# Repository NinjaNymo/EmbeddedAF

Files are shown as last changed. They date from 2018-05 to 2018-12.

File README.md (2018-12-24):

# EmbeddedAF
This repository contains the source code and hardware design files for a indoor automated urban farming system. 

The system has a master/slave architecture, where the master is refered to as the _master_, while the slaves as the _nodes_.

### **_The Concept:_**
The idea was to use a wireless sensor network system as a case study in an embedded systems development process.

Due to the master/slave architecture of the system, the project covers both embedded C development on the node devices and embedded Linux development on the master device, as well as communication over ZigBee between the two.

All in all; a good variation of challanges to learn more about embedded systems.

### **_The Node:_**
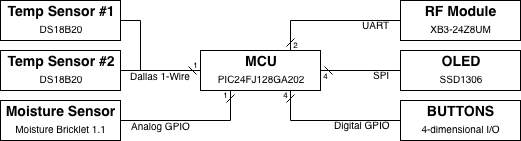
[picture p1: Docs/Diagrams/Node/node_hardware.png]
Node Structure


The node features a 16-bit MCU and a XBee 3 ZigBee module on an in-house developed and etched PCB. An OLED display and buttons are included on the board such that the node device can be used in an _offline mode_ independetly of the master device.

The node device measures temperature on the PCB and interfaces with 1) external digital temperature sensors, 2) an external analog soil moisture sensor and 3) an external relay that controls a grow-light.

The idea is to control the grow-light on a day/night-like cycle and record and publish the temperature and soil moisture measurements to the master device.

* The firmware is written in C, and can be found in [/src/node/](/src/node).
* The schematic and PCB is designed in Eagle, and can be found in [/Eagle/node/](/Eagle/node/).

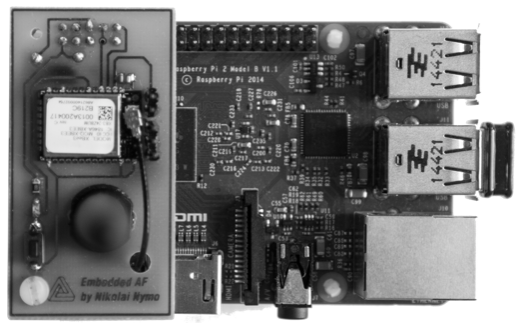
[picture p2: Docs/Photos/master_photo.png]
Master PCB
 

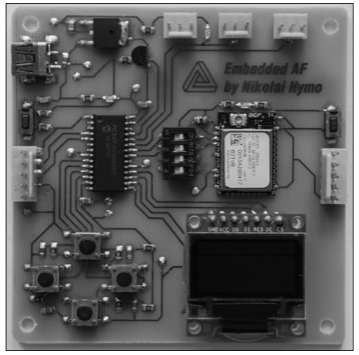
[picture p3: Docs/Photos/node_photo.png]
Node PCB Node PCB


Master Structure
This repository contains stuff for a project on embedded automatic farming.

That includes circuit schematics, PCB designs and code to run on the two systems:

1. **The node:** A board with a 16-bit MCU and a XBee 3 micro module. It features two temperature sensors and one analog soil moisture sensor as well as I/O for offline availiability. The source found in src/node is written C and compiles with XC16.
2. **The master:** A Raspberry Pi 2B mounted with the same XB3 modules as the nodes. It runs Raspbian Stretch lite, a MQTT broker, a Node.js server that provides a web ui and finally a MQTT-SN gateway that is implemented in python and who's source code is found in src/master.

In addition there are some random python scripts, diagrams in the DrawIO folder, prototype schematics and board designs.

### The concept:

The idea here is to use a wireless sensor network system inteded to be used in indoor automatic farming as a case study in a development process.

I like watching things grow, and I think indoor has interesting benefits over traditional outdoor farming such as reduced water consumption, seasonal independence and a shorter logistic travel distance so perhaps some day all this might turn into something.

To do automated farming, it controls a LED lamp on a day/night-like cycle which can be configured through the on-board user interface or wirelessly.

The lamp and power distribution needs some work and will be put up here once it is up to spec. 

Further the node measures water content in soil which is intended to be used with automated watering. It has a Dallas 1-wire bus on one of it connectors which currently run both an on-board temp sensor and an external waterproof one that I planned on sticking in the soil.

The MCU does everything mentioned above, and UARTs with the XB3 which handle MQTT over ZigBee.

With many of these and an online master device from which you can monitor and control the whole setup it should be possible to realize indoor automated farming.

### Technical details:

#### The node:
* Microchip PIC24FJ128GA202 MCU. 16-bit.
* Digi XB3-24Z8UM RF module running ZigBee 3.0 API as a router.
* Maxim DS18B20 temperature sensors.
* Analog capacative soil moisture sensor.
* SSD1306 OLED display driver.
*

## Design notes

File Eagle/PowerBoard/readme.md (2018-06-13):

### Resources:
* [Relay switch circuits.](https://www.electronics-tutorials.ws/blog/relay-switch-circuit.html)
* [G5LE relay @ DigiKey.](https://www.digikey.com/product-detail/en/omron-electronics-inc-emc-div/G5LE-14-DC3/Z3326-ND/1815628)

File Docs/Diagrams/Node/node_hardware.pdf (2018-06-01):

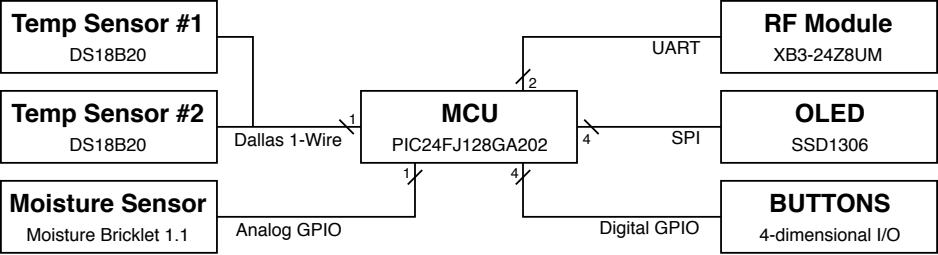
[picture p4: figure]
MCU; PIC24FJ128GA202; RF Module; Temp Sensor #1; Temp Sensor #2; Analog GPIO; Moisture Sensor; Moisture Bricklet 1.1; OLED; SSD1306; BUTTONS; 4-dimensional I/O; Dallas 1-Wire; SPI 4; Digital GPIO; UART

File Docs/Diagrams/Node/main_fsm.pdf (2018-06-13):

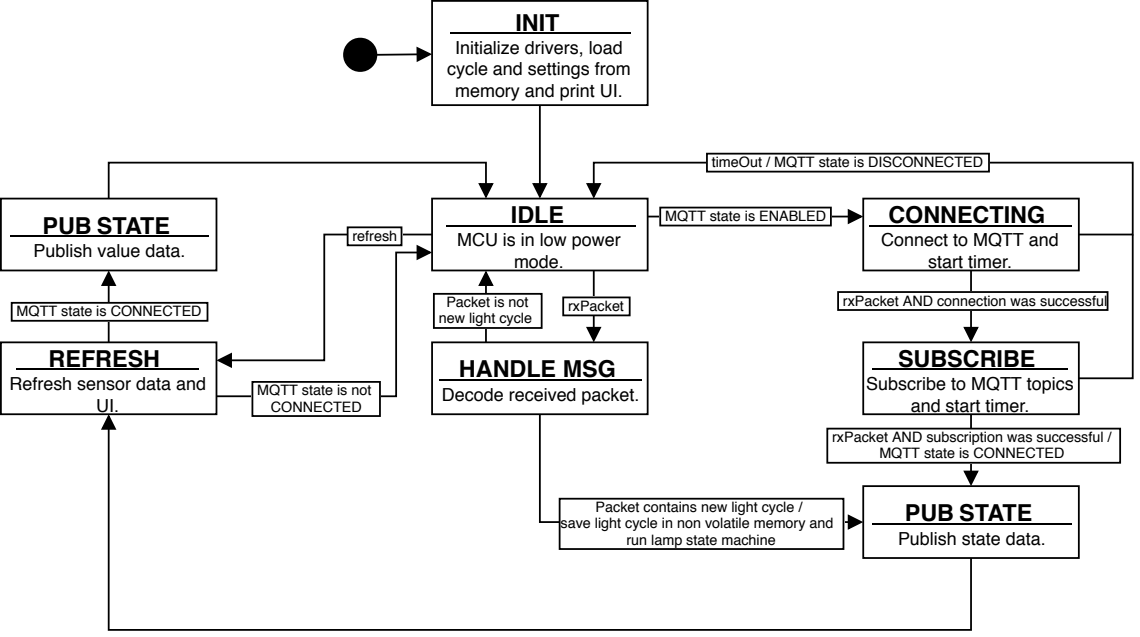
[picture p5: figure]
MQTT state is ENABLED; rxPacket; refresh; IDLE; MCU is in low power mode.; rxPacket AND connection was successful; timeOut / MQTT state is DISCONNECTED; CONNECTING; Connect to MQTT and start timer.; MQTT state is CONNECTED; SUBSCRIBE; Subscribe to MQTT topics and start timer.; PUB STATE; Publish state data.; Packet is not new light cycle; Packet contains new light cycle /; run lamp state machine; HANDLE MSG; Decode received packet.; MQTT state is not CONNECTED; REFRESH; Refresh sensor data and UI.; Publish value data.; INIT; Initialize drivers, load cycle and settings from memory and print UI.

rxPacket AND subscription was successful /

save light cycle in non volatile memory and

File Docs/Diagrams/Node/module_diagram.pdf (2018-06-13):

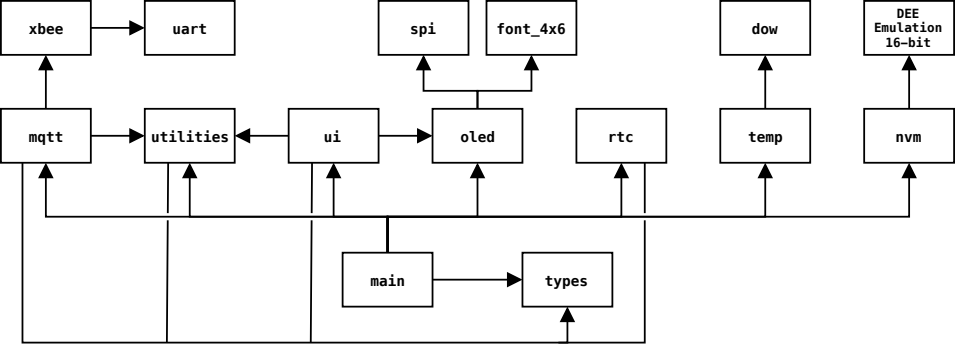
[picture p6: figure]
spi; oled; dow; temp; xbee; mqtt; utilities; rtc; uart; nvm; DEE Emulation 16-bit; font_4x6; main; types

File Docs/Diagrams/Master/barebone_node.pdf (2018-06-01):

MCU
Microchip
PIC24FJ128GA202

RF Module
Digi
XB3-24Z8UM

Temperature 1
Maxim Integrated
DS18B20

Temperature 2
Maxim Integrated
DS18B20

Water
Tinkerforge
Moisture Bricklet 1.1

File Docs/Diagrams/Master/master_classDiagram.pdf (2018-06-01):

«Class»
digi:xbee:devices:ZigBeeDevice
on_connect | : function*
on_message | : function*
on_subscribe : function*
on_disconnect : function*
__init__(port:string, baud_rate:integer)
open()
add_data_received_callback(function*) send_data(remote_xbee_device:ZigBeeDevice, data:bytearray) get_64bit_addr() : bytearray

«Class»
lib:threading:Thread
daemon : bool
name : string
start()

«Class»
MSG
sender : ZigBeeDevice
data : bytearray

«Class»
Gateway
inQ | : Queue
outQ | : Queue
XBH | : XBeeHandler
clientList : NodeClient[0..*] __init__(uartPort:string)
start()
stop()

«Class»
NodeClient
inQ | : Queue
outQ | : Queue
stop | : bool
nodeID : string
device : ZigBeeDevice
mClient : Client
__init__(device:ZigBeeDevice, outQ:Queue, nodeID:string)
run()
connect(keepAlive:integer)
connectedCB(client:Client, userdata:null, flags:dict, rc:integer) subscribe(topic:string)
subscribedCB(client:Client, userdata:null, mid:integer, granted_qos:integer) publish(msg:MSG)
messageCB(client:Client, userdata:null, msg:mqtt_msg)
disconnect()
disconnectedCB(client:Client, userdata:null, rc:integer) put(msg:MSG)
terminate()

«Class»
XBeeHandler
inQ | : Queue
outQ | : Queue
device : ZigBeeDevice
__init__(inQ:Queue, outQ:Queue, XBeePort:string) run()
receiveCB(xbee_message:XBeeMessage) terminate()

«Class»
paho:mqtt:client:Client
on_connect | : function*
on_message | : function*
on_subscribe : function*
on_disconnect : function*
connect(host:string, port:integer, keepAlive:integer) subscribe(topic:string)
publish(topic:string, data:integer) publish(topic:string, data:string)
loop_start()
loop_stop()
disconnect()
1 | 1 | 1 | 1
1 | 0..*

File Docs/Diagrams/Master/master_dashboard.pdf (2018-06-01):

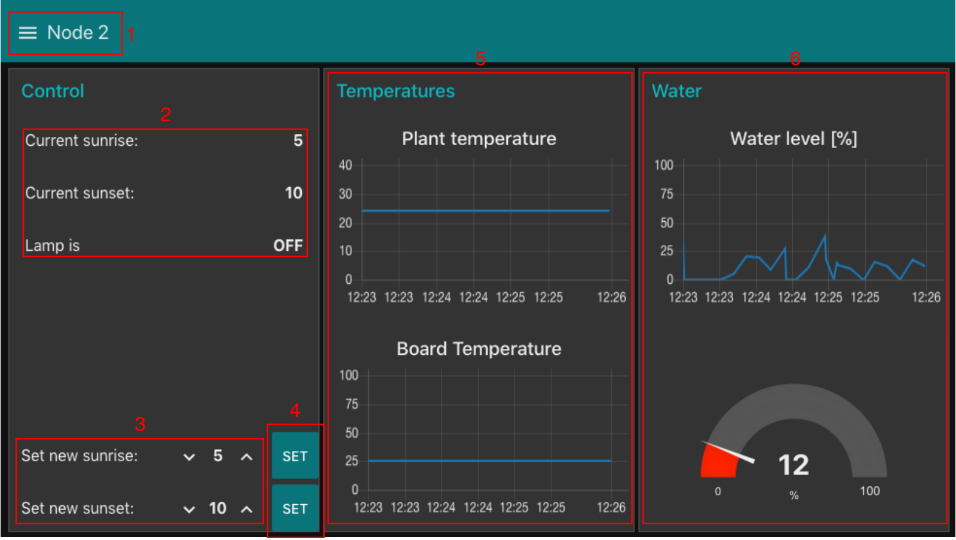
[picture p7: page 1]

1

2

3

4

5

6

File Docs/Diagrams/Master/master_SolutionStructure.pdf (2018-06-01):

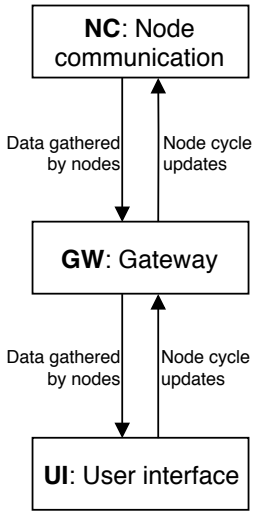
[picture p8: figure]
NC: Node communication; GW: Gateway; UI: User interface; Node cycle updates; Data gathered by nodes

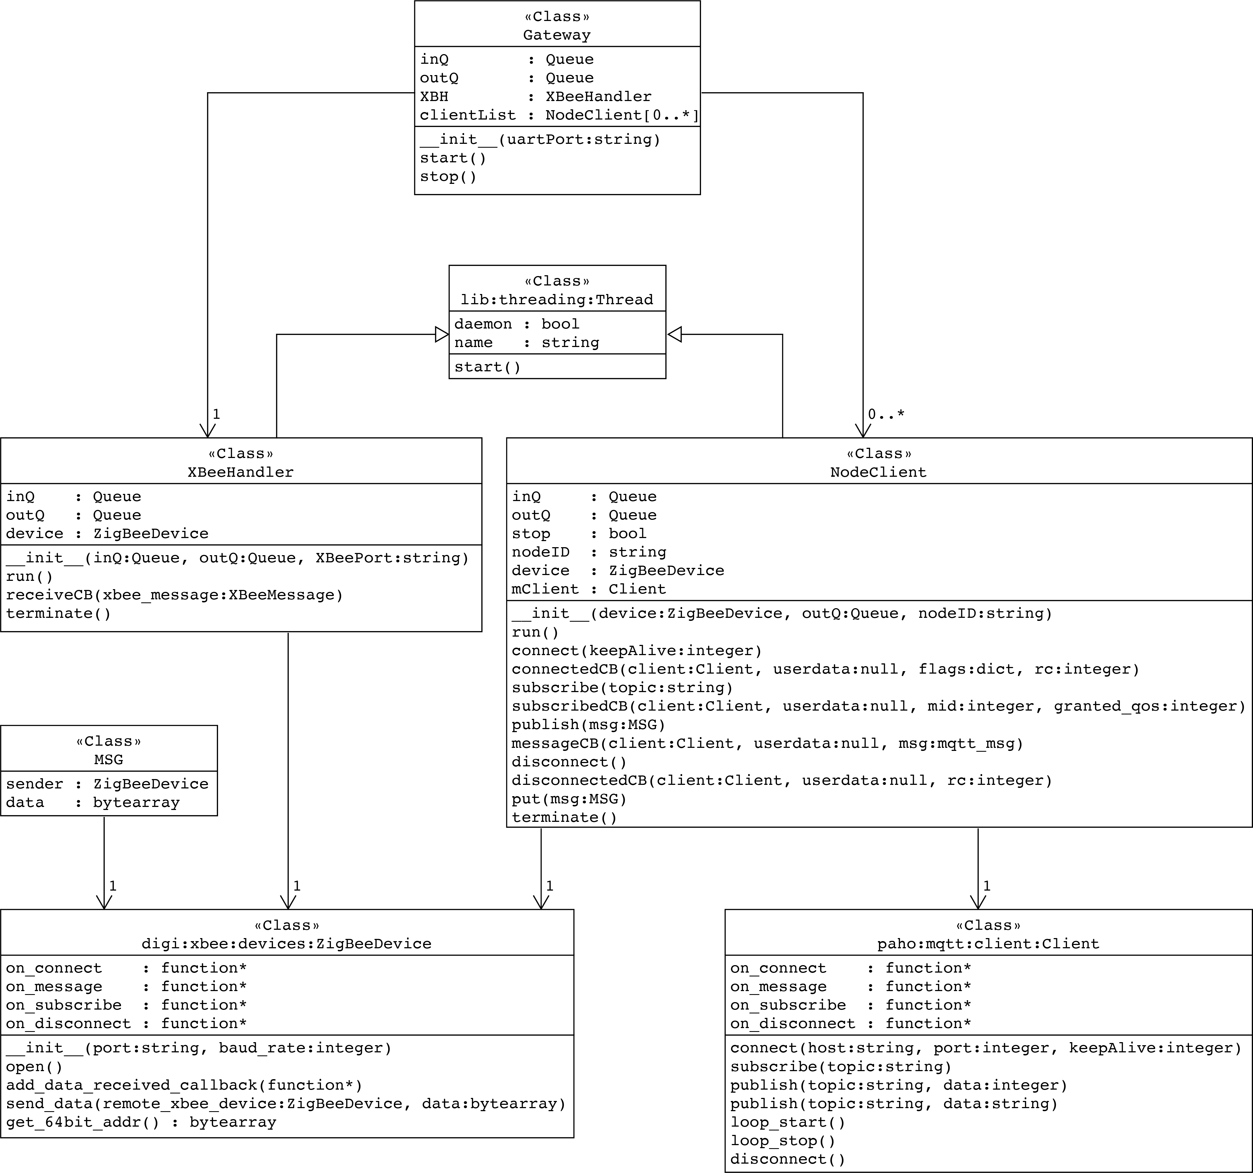
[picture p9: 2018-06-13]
Docs/Diagrams/Master/master_classDiagram.png

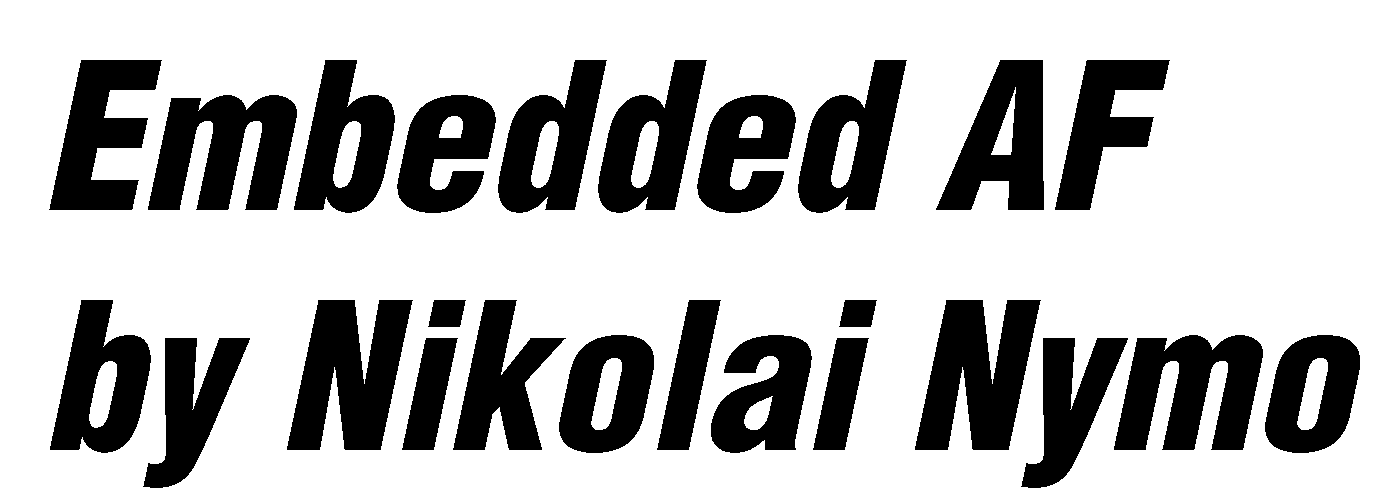
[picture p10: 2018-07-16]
Eagle/Bitmaps/EAF.bmp

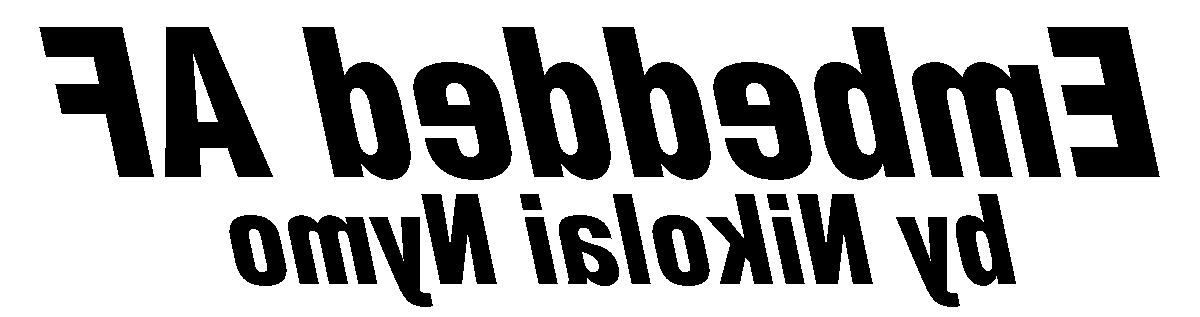
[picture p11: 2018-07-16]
Eagle/Bitmaps/EmbeddedAF.bmp

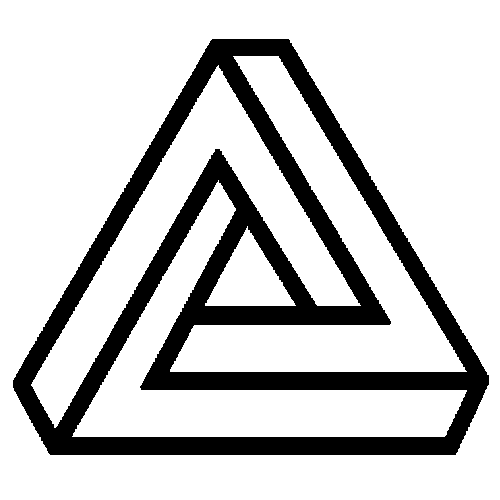
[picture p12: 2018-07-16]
Eagle/Bitmaps/penrose.bmp

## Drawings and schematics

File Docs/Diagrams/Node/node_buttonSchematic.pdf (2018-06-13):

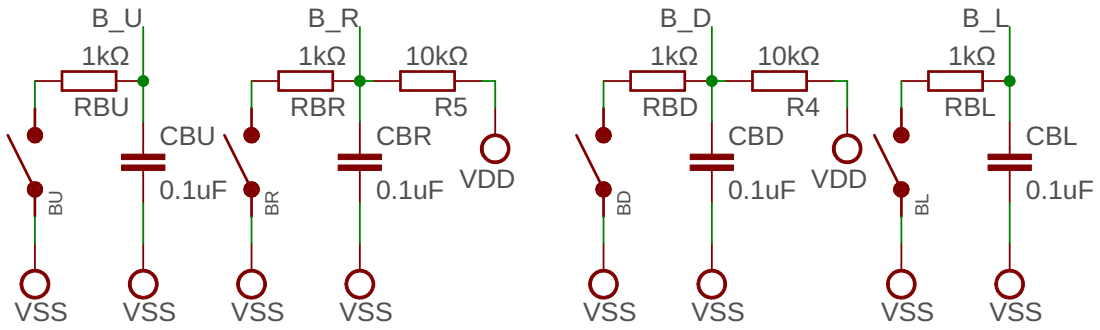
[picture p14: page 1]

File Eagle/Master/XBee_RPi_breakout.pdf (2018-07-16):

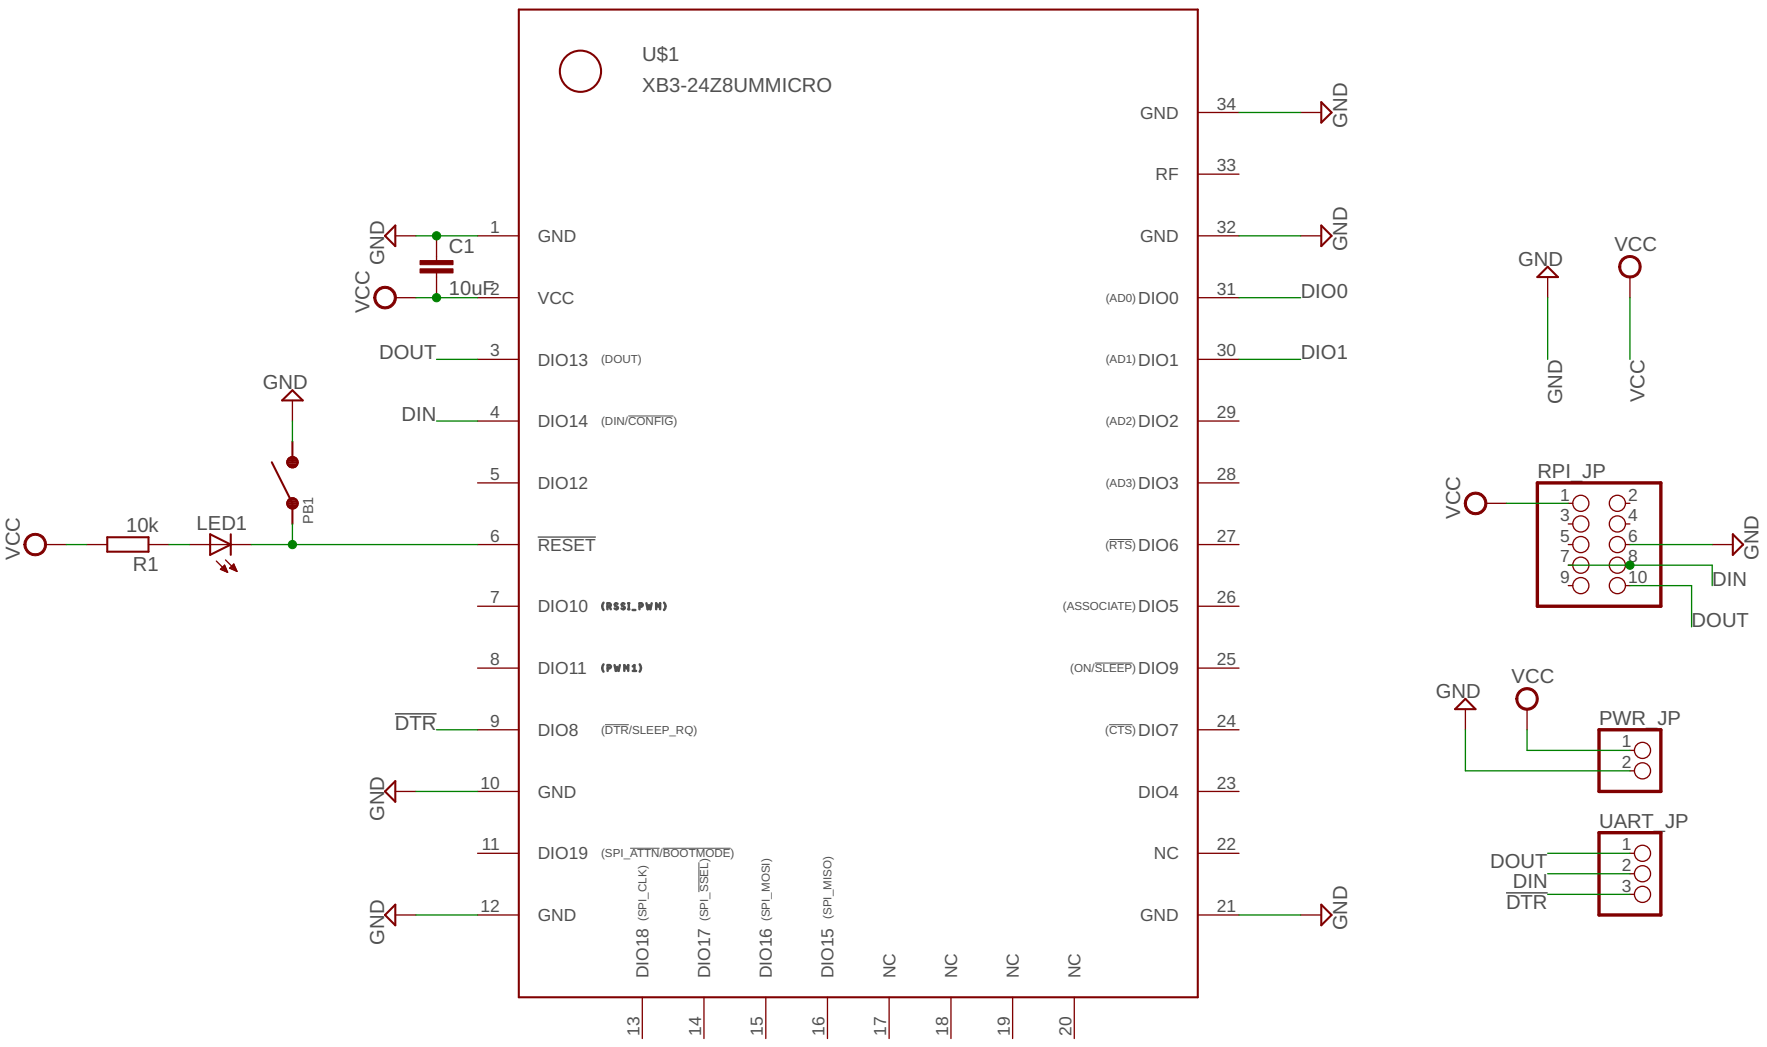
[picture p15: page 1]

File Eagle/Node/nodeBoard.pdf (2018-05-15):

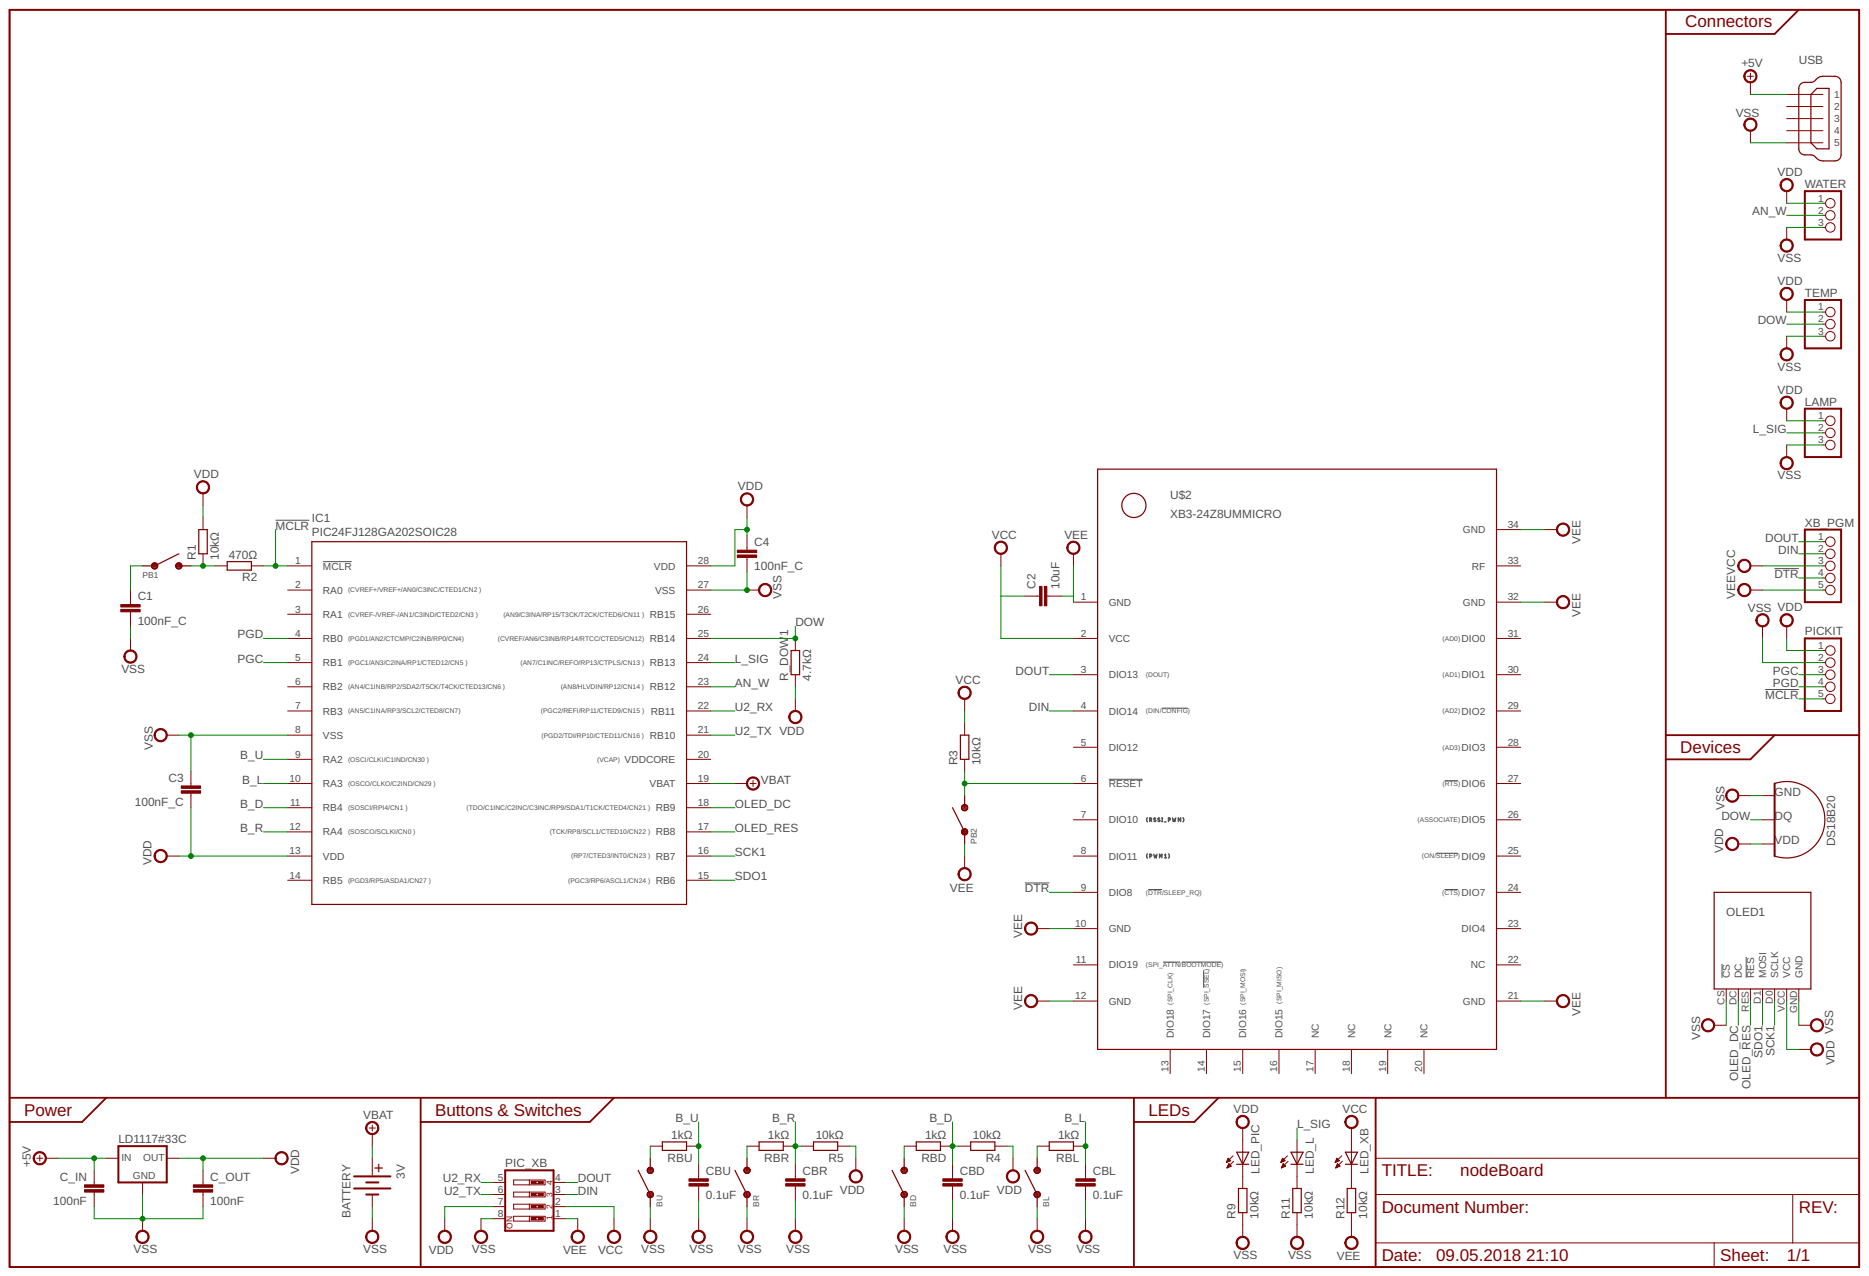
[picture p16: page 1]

RES RES MOSI D1 SCLK D0 VCC

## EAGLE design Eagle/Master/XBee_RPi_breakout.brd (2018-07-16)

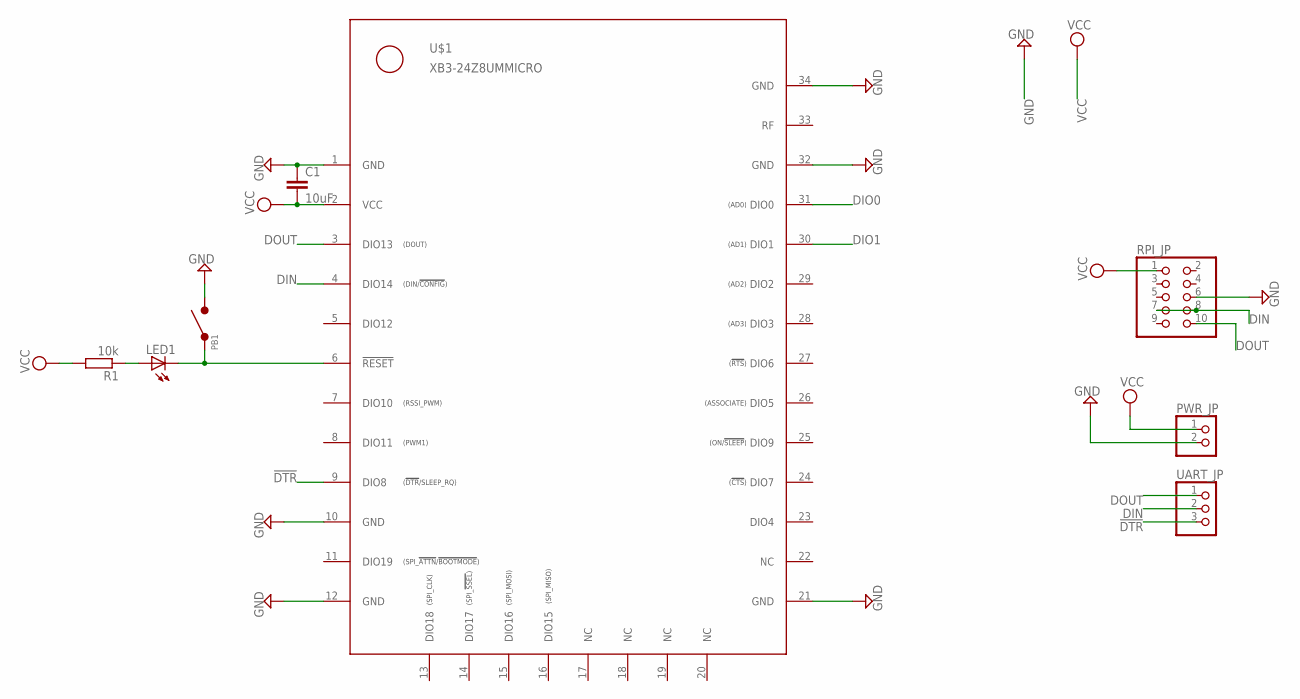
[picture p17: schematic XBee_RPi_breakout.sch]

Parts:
C1: 10uF; C0805
LED1: LEDSML0805; SML0805
PB1: PUSHBUTTON_2LEG; PUSHBUTTON_6X3.5MM
PWR_JP: PINHD-1X2; 1X02
R1: 10k; M0805
RPI_JP: PINHD-2X5; 2X05
U$1: XB3-24Z8UMMICRO; XBEE3_MICRO
UART_JP: PINHD-1X3; 1X03

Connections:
!DTR: U$1.9 (DIO8), UART_JP.3
!RST: LED1.C, PB1.P$1, U$1.6 (!RESET)
DIN: RPI_JP.7, RPI_JP.8, U$1.4 (DIO14), UART_JP.2
DIO0: U$1.31 (DIO0)
DIO1: U$1.30 (DIO1)
DOUT: RPI_JP.10, U$1.3 (DIO13), UART_JP.1
GND: C1.1, PB1.P$2, PWR_JP.2, RPI_JP.6, U$1.1 (GND), U$1.10 (GND), U$1.12 (GND), U$1.21 (GND), U$1.32 (GND), U$1.34 (GND)
unnamed: LED1.A, R1.1
VCC: C1.2, PWR_JP.1, R1.2, RPI_JP.1, U$1.2 (VCC)

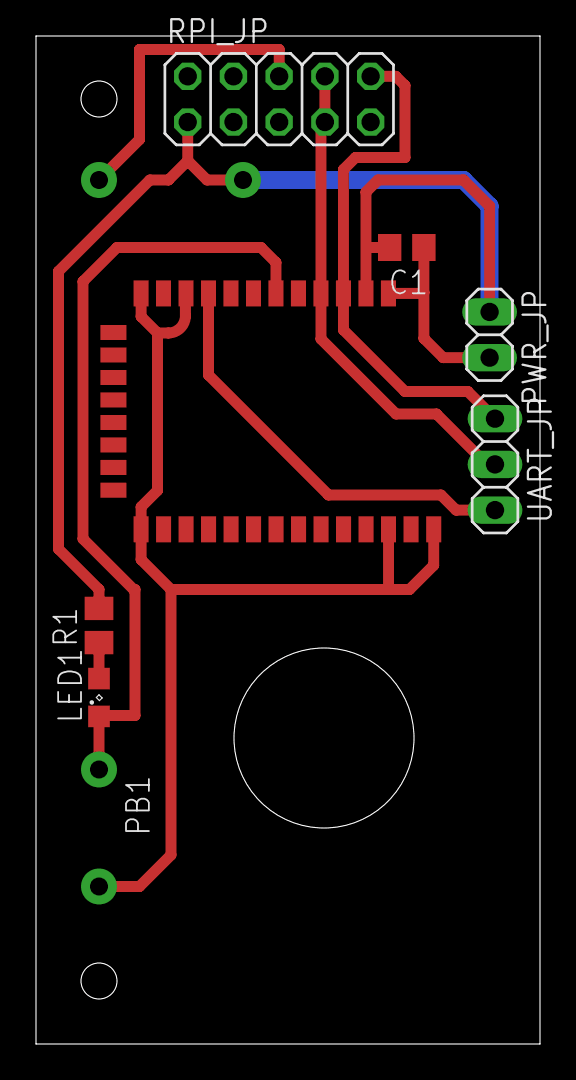
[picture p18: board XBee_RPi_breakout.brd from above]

Board: 2 copper layers, 28.0 x 56.0 mm, 8 parts (0 on the bottom side), 7 nets.

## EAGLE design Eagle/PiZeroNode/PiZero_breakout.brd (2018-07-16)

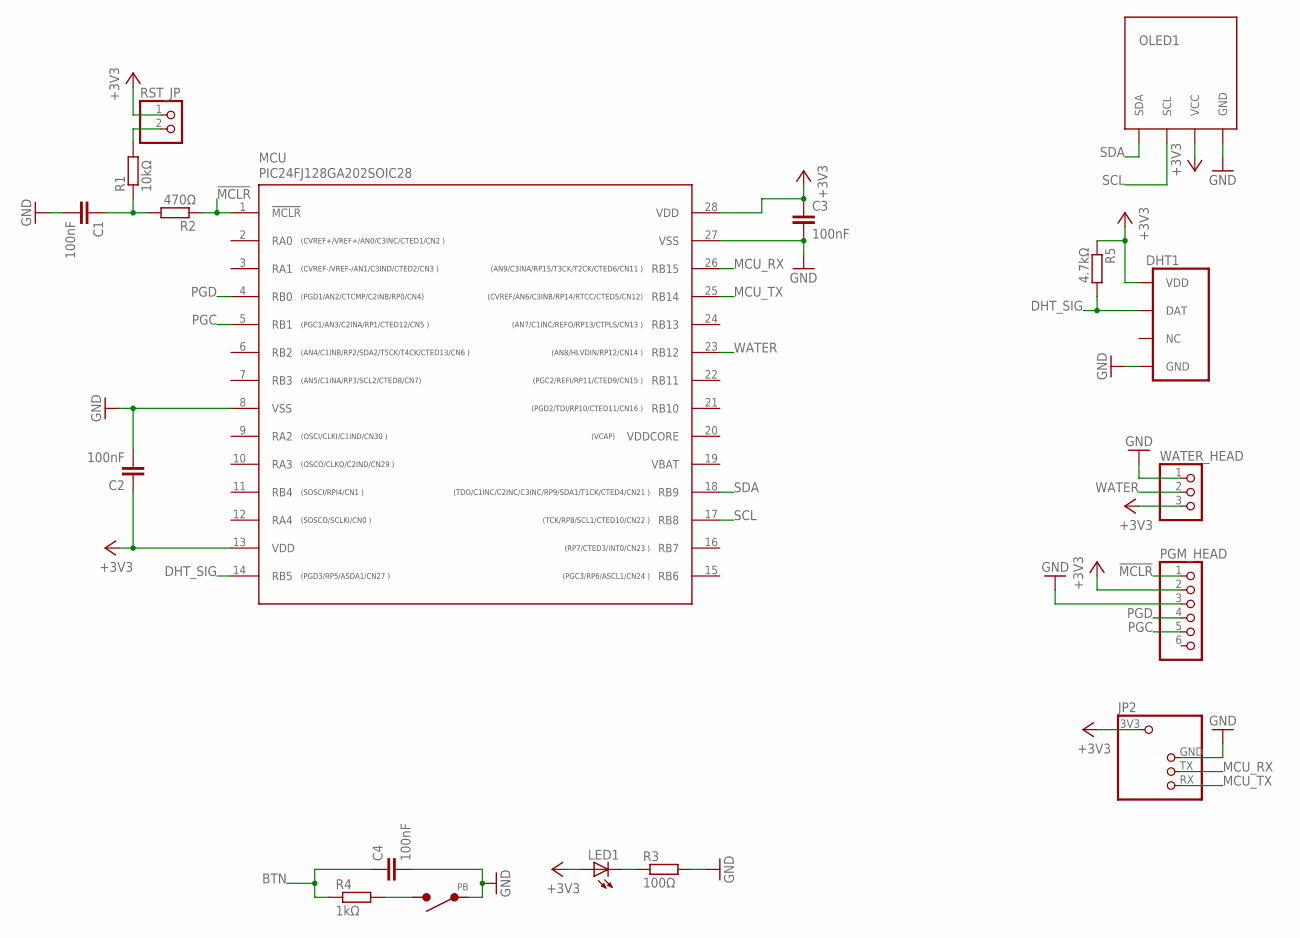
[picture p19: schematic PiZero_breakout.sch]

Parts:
C1, C2, C3, C4: 100nF; C0805
DHT1: DHT11VERT; DHT11
JP2: RPI_UART_HEADER; RPI_UART_HEAD
LED1: LEDCHIPLED_0805; CHIPLED_0805
MCU: PIC24FJ128GA202SOIC28; SOIC28L
OLED1: OLED_4PIN_I2C; OLED_4PIN
PB: PUSHBUTTON_2LEG; PUSHBUTTON_6X3.5MM
PGM_HEAD: PINHD-1X6; 1X06
R1: 10kΩ; R0805
R2: 470Ω; R0805
R3: 100Ω; R0805
R4: 1kΩ; R0805
R5: 4.7kΩ; R0805
RST_JP: PINHD-1X2; 1X02
WATER_HEAD: PINHD-1X3; 1X03

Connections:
!MCLR: MCU.1 (!MCLR), PGM_HEAD.1, R2.1
+3V3: C2.1, C3.1, DHT1.VDD, JP2.3V3, LED1.A, MCU.13 (VDD), MCU.28 (VDD), OLED1.VCC, PGM_HEAD.2, R5.1, RST_JP.1, WATER_HEAD.3
BTN: C4.1, R4.1
DHT_SIG: DHT1.DAT, MCU.14 (RB5), R5.2
GND: C1.2, C2.2, C3.2, C4.2, DHT1.GND, JP2.GND, MCU.8 (VSS), MCU.27 (VSS), OLED1.GND, PB.P$1, PGM_HEAD.3, R3.2, WATER_HEAD.1
MCU_RX: JP2.TX, MCU.26 (RB15)
MCU_TX: JP2.RX, MCU.25 (RB14)
unnamed: C1.1, R1.1, R2.2
unnamed: LED1.C, R3.1
unnamed: R1.2, RST_JP.2
unnamed: PB.P$2, R4.2
PGC: MCU.5 (RB1), PGM_HEAD.5
PGD: MCU.4 (RB0), PGM_HEAD.4
SCL: MCU.17 (RB8), OLED1.SCL
SDA: MCU.18 (RB9), OLED1.SDA
VDDCORE: MCU.20 (VDDCORE)
WATER: MCU.23 (RB12), WATER_HEAD.2

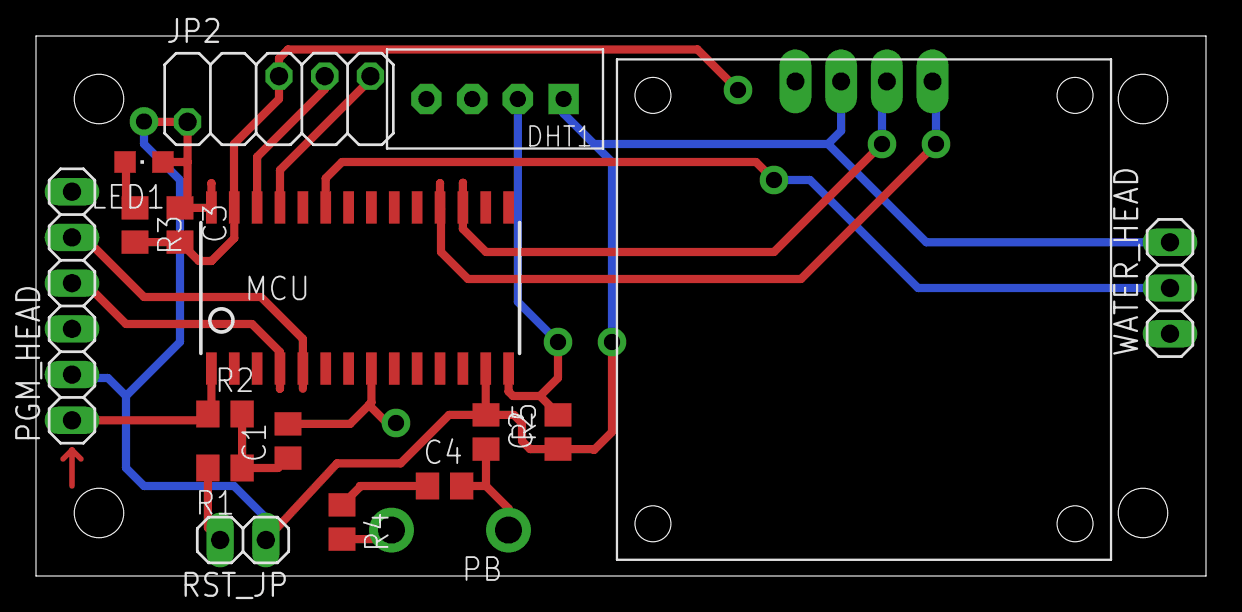
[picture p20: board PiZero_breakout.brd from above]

Board: 2 copper layers, 65.0 x 30.0 mm, 18 parts (0 on the bottom side), 16 nets.

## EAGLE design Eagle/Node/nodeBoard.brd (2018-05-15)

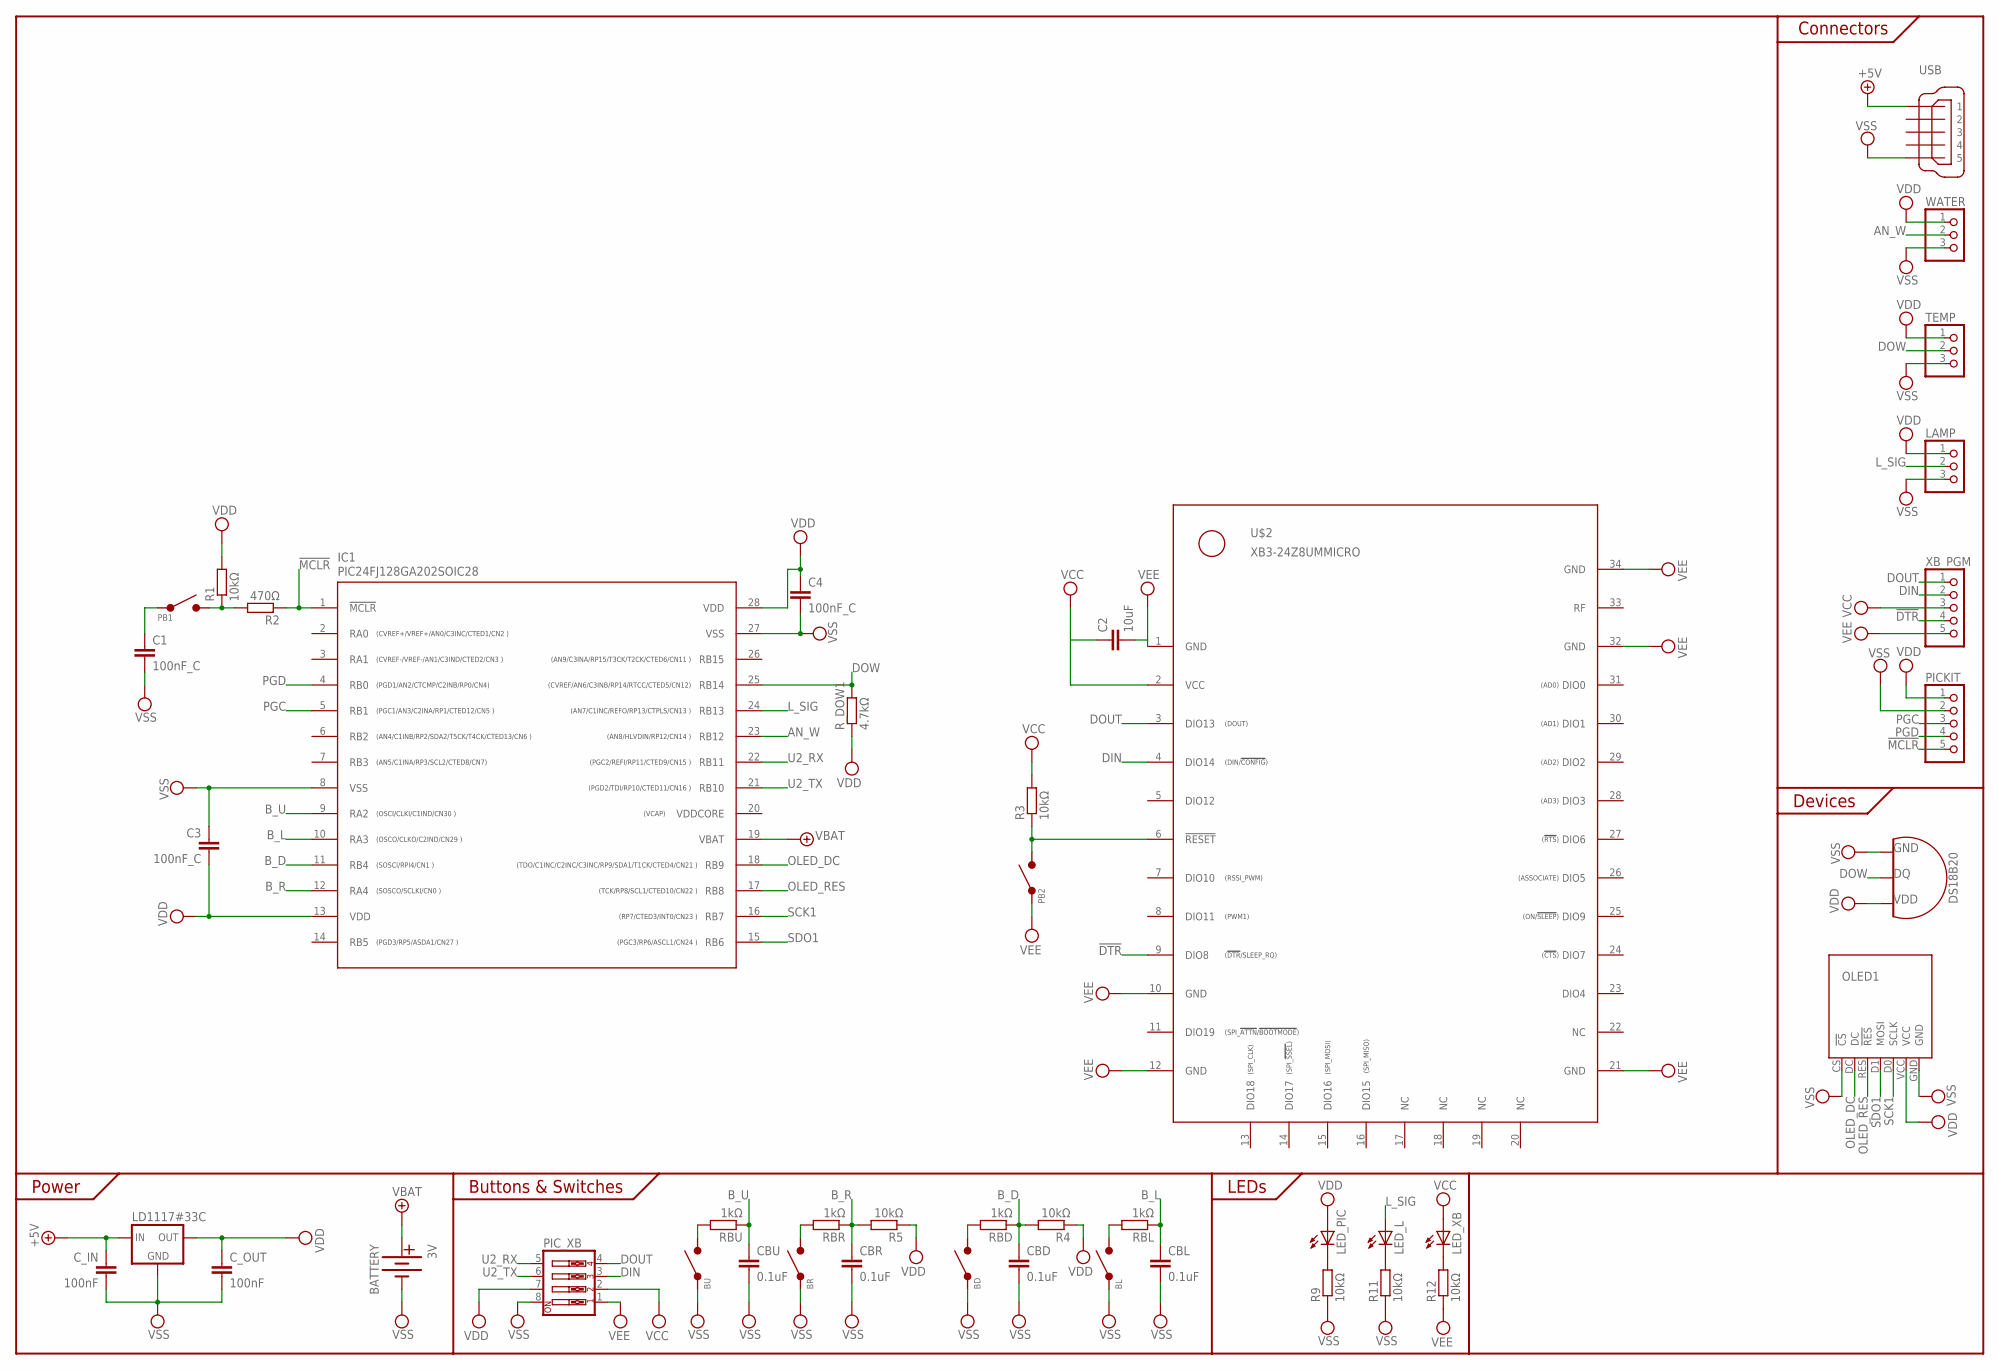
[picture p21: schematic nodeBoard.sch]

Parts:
3V: BATTERY; 20MM_CELLHOLDER
BD: PUSHBUTTON_4LEG_SMD; TACTILE_SWITCH_SMD_6.2MM_BROWN
BL: PUSHBUTTON_4LEG_SMD; TACTILE_SWITCH_SMD_6.2MM_BROWN
BR: PUSHBUTTON_4LEG_SMD; TACTILE_SWITCH_SMD_6.2MM_BROWN
BU: PUSHBUTTON_4LEG_SMD; TACTILE_SWITCH_SMD_6.2MM_BROWN
C1, C3, C4: 100nF_C; C0805
C2: 10uF; C0805
CBD: 0.1uF; C0805
CBL: 0.1uF; C0805
CBR: 0.1uF; C0805
CBU: 0.1uF; C0805
C_IN: 100nF; C0805
C_OUT: 100nF; C0805
IC1: PIC24FJ128GA202SOIC28; SOIC28L
LAMP: PINHD-1X3; 1X03
LED_L: LEDCHIPLED_0805; CHIPLED_0805
LED_PIC: LEDCHIPLED_0805; CHIPLED_0805
LED_XB: LEDCHIPLED_0805; CHIPLED_0805
OLED1: OLED_7PIN_SPI; OLED_7PIN
PB1, PB2: PUSHBUTTON_2LEG; PUSHBUTTON_6X3.5MM
PICKIT: PINHD-1X5; 1X05
PIC_XB: SW_DIP-4; EDG-04
R1, R3, R4, R5, R9, R11, R12: 10kΩ; R0805
R2: 470Ω; R0805
RBD: 1kΩ; R0805
RBL: 1kΩ; R0805
RBR: 1kΩ; R0805
RBU: 1kΩ; R0805
R_DOW1: 4.7kΩ; R0805
TEMP: PINHD-1X3; 1X03
U$1: LD1117#33C; DPACK
U$2: XB3-24Z8UMMICRO; XBEE3_MICRO
U$7: DS18B20; TO92
USB: MINI-USB-32005-201; 32005-201
WATER: PINHD-1X3; 1X03
XB_PGM: PINHD-1X5; 1X05

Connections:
!DTR: U$2.9 (DIO8), XB_PGM.4
!MCLR: IC1.1 (!MCLR), PICKIT.5, R2.1
+5V: C_IN.1, U$1.3 (IN), USB.1
AN_W: IC1.23 (RB12), WATER.2
B_D: CBD.1, IC1.11 (RB4), R4.2, RBD.1
B_L: CBL.1, IC1.10 (RA3), RBL.1
B_R: CBR.1, IC1.12 (RA4), R5.2, RBR.1
B_U: CBU.1, IC1.9 (RA2), RBU.1
DIN: PIC_XB.3, U$2.4 (DIO14), XB_PGM.2
DOUT: PIC_XB.4, U$2.3 (DIO13), XB_PGM.1
DOW: IC1.25 (RB14), R_DOW1.2, TEMP.2, U$7.2 (DQ)
L_SIG: IC1.24 (RB13), LAMP.2, LED_L.A
unnamed: C1.1, PB1.P$1
unnamed: PB2.P$2, R3.1, U$2.6 (!RESET)
unnamed: PB1.P$2, R1.1, R2.2
unnamed: BU.B1, BU.B2, RBU.2
unnamed: BL.B1, BL.B2, RBL.2
unnamed: BR.B1, BR.B2, RBR.2
unnamed: BD.B1, BD.B2, RBD.2
unnamed: LED_L.C, R11.2
unnamed: LED_XB.C, R12.2
unnamed: LED_PIC.C, R9.2
OLED_DC: IC1.18 (RB9), OLED1.DC
OLED_RES: IC1.17 (RB8), OLED1.RES (!RES)
PGC: IC1.5 (RB1), PICKIT.3
PGD: IC1.4 (RB0), PICKIT.4
SCK1: IC1.16 (RB7), OLED1.D0 (SCLK)
SDO1: IC1.15 (RB6), OLED1.D1 (MOSI)
U2_RX: IC1.22 (RB11), PIC_XB.5
U2_TX: IC1.21 (RB10), PIC_XB.6
VBAT: 3V.+@1 (+), 3V.+@2 (+), IC1.19 (VBAT)
VCC: C2.1, LED_XB.A, PIC_XB.2, R3.2, U$2.2 (VCC), XB_PGM.3
VDD: C3.2, C4.1, C_OUT.1, IC1.13 (VDD), IC1.28 (VDD), LAMP.1, LED_PIC.A, OLED1.VCC, PICKIT.1, PIC_XB.7, R1.2, R4.1, R5.1, R_DOW1.1, TEMP.1, U$1.2 (OUT), U$7.3 (VDD), WATER.1
VDDCORE: IC1.20 (VDDCORE)
VEE: C2.2, PB2.P$1, PIC_XB.1, R12.1, U$2.1 (GND), U$2.10 (GND), U$2.12 (GND), U$2.21 (GND), U$2.32 (GND), U$2.34 (GND), XB_PGM.5
VSS: 3V.-, BD.A1, BD.A2, BL.A1, BL.A2, BR.A1, BR.A2, BU.A1, BU.A2, C1.2, C3.1, C4.2, CBD.2, CBL.2, CBR.2, CBU.2, C_IN.2, C_OUT.2, IC1.8 (VSS), IC1.27 (VSS), LAMP.3, OLED1.CS (!CS), OLED1.GND, PICKIT.2, PIC_XB.8, R9.1, R11.1, TEMP.3, U$1.1 (GND), U$7.1 (GND), USB.5, WATER.3

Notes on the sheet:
Power
Connectors
Buttons & Switches
Devices
LEDs

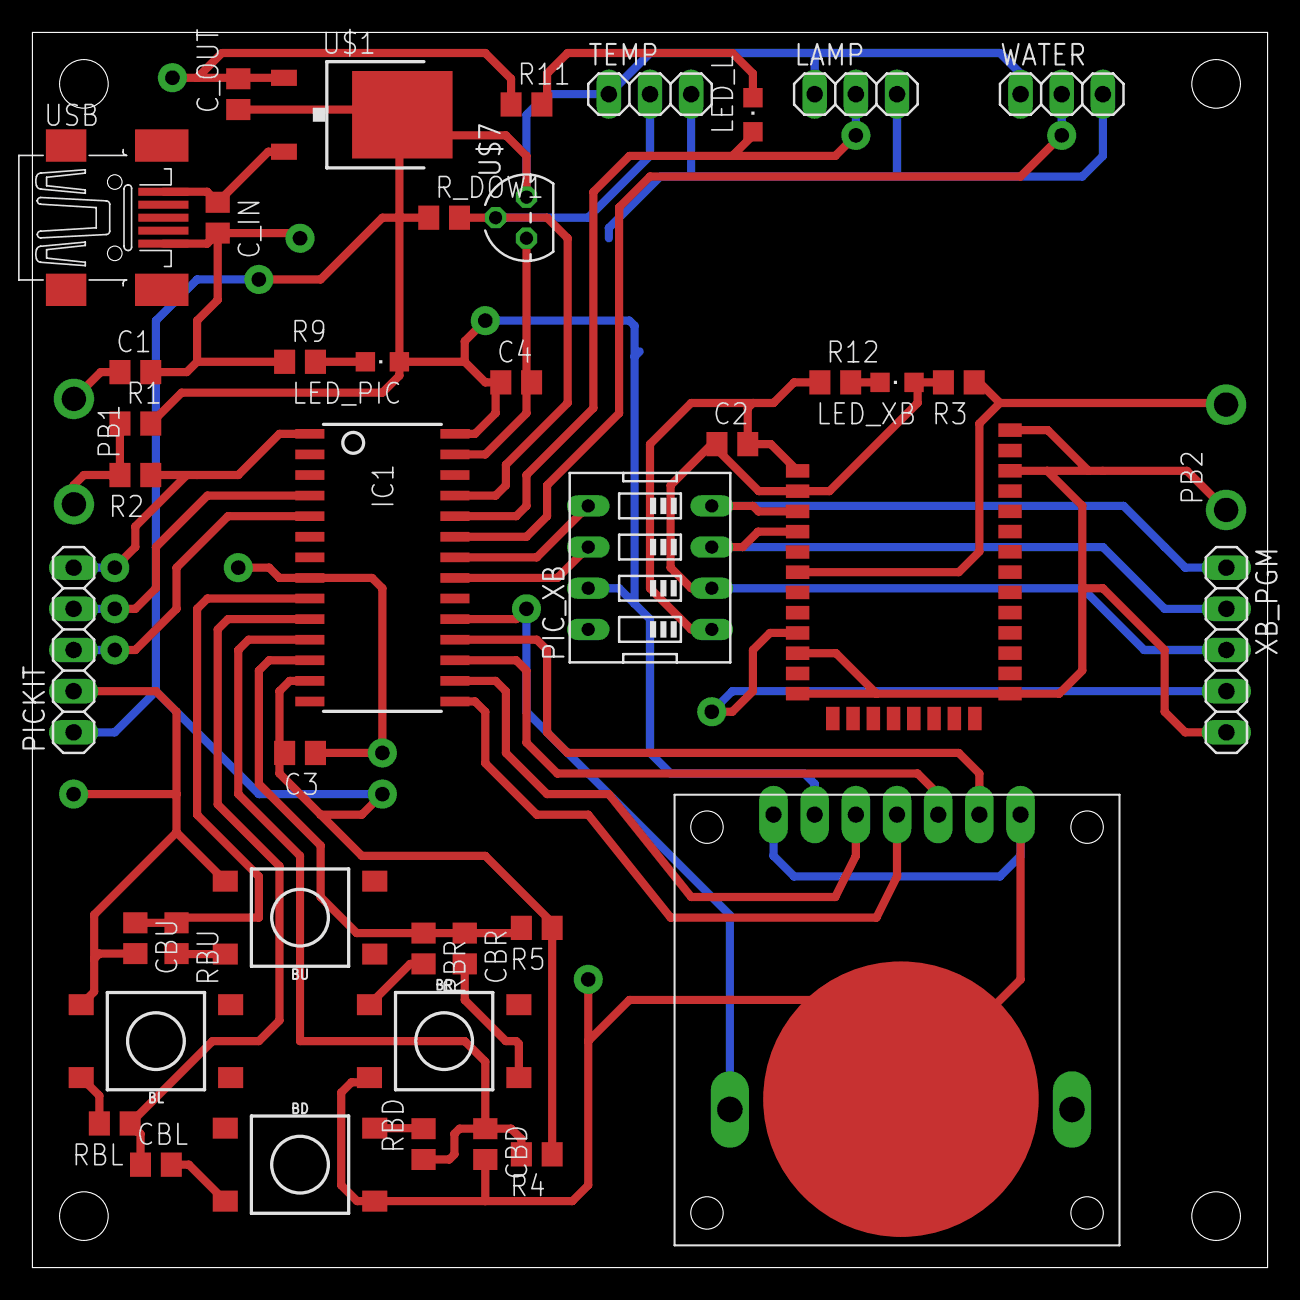
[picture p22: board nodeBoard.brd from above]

Board: 2 copper layers, 76.2 x 76.2 mm, 45 parts (0 on the bottom side), 35 nets.

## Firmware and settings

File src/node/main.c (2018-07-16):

//   _____ _____ _____
//  |   | |__   |   | | EmbeddedAF/src/node/main.c
//  | | | |   __| | | | Nikolai Nymo
//  |_|___|_____|_|___| 06-02-18
#include <xc.h>
#define FCY 4000000L // Define before including libpic
#include <libpic30.h>
#include "types.h"
#include "utilities.h"
#include "uart.h"
#include "oled.h"
#include "rtc.h"
#include "temp.h"
#include "ui.h"
#include "nvm.h"
#include "mqtt.h"

#include "stdio.h"
//-----------------------------------------------//
//                    DEFINES                    //                     
//-----------------------------------------------//
#define REFRESHITIME 0b0010 // 0b0 = 1s, 0b10 = 10s, 0b100 = 1h
                            // Count with ISR for more...

#define ISR __attribute__((interrupt, auto_psv))
//-----------------------------------------------//
//                    GLOBALS                    //                     
//-----------------------------------------------//
systemState_t state = {INIT, 0, 0, {0}, {0, 0, 0}, 0, 0, 0, OFF, DISABLED, {0, 0, 0, 0}, NONE};
//-----------------------------------------------//
//               INPUT CHANGE ISR                //                     
//-----------------------------------------------//
void ISR _CNInterrupt(){
    if(PORTAbits.RA2 == 0){
        state.bDir = UP;
        state.flags.bChange = 1;
    }
    else if(PORTAbits.RA3 == 0){
        state.bDir = LEFT;
        state.flags.bChange = 1;
    }
    else if(PORTBbits.RB4 == 0){
        state.bDir = DOWN;
        state.flags.bChange = 1;
    }
    else if(PORTAbits.RA4 == 0){
        state.bDir = RIGHT;
        state.flags.bChange = 1;
    }
    IFS1bits.CNIF = 0; // Clear the flag
}
//-----------------------------------------------//
//               TIMER 2/3 ISR                   //                     
//-----------------------------------------------//
void ISR _T3Interrupt(){
    state.flags.timeOut = 1; // Set the time-out flag
    IFS0bits.T3IF       = 0; // Clear the flag
}
//-----------------------------------------------//
//               RTC ALARM ISR                   //                     
//-----------------------------------------------//

void ISR _RTCCInterrupt(){
    state.flags.refresh = 1; // Set the time-out flag
    IFS3bits.RTCIF      = 0; // Clear the flag
}
//-----------------------------------------------//
//                 U1 RX ISR                     //                     
//-----------------------------------------------//
volatile uint8_t packet[30];
volatile uint16_t pIndex = 0;
volatile uint16_t pLength = 0;
void ISR _U1RXInterrupt(){
    IFS0bits.U1RXIF = 0;
    uint8_t rx = U1RXREG;
    
    // Look for start of new message:
    if((rx == 0x7E) && (pIndex == 0)){
        packet[0] = 0x7E;
        pIndex = 1;
    }
    else if(pIndex != 0){
        packet[pIndex] = rx;
        if(pIndex == 1){
            pLength = rx << 8;
            pIndex ++;
        }
        else if(pIndex == 2){
            pLength += rx;
            pIndex ++;
        }
        // Look for end of message:
        else{
            pIndex ++;
            if(pIndex == (pLength + 4)){
                pIndex = 0;
                pLength += 4;
                state.flags.rxPacket = 1;
            }
        }      
    }
}
//-----------------------------------------------//
//             PRIVATE FUNCTIONS                 //                     
//-----------------------------------------------//
static void refreshState(){            
    state.time = rtc_getTime();
    util_runLampFSM(&state);
    temp_startConversion();
    __delay_ms(10);
    state.boardTemp = temp_getTemp(probe);
    state.plantTemp = temp_getTemp(wireProbe);
    state.waterLevel = util_getWaterLevel();
}

static void initAll(){
    util_initPins();
    util_initADC();
    util_initTimer23();
    uart_init9600(1); // Channel 1
    util_initInterrupts();
    oled_init();
    rtc_init(REFRESHITIME); 
    nvm_init();
    
}

void test(){
    initAll();
    oled_printChar('X');
    util_startTimer23();
    while(1);
}
//-----------------------------------------------//
//                    MAIN                       //                     
//-----------------------------------------------//
int main(void){
    while(1){
        switch(state.loopState){
            case INIT:
                initAll();
                // Load cycle and settings from memory:
                uint16_t cycle = nvm_getCycle();
                state.sunset = cycle & 0xFF;
                state.sunrise = (cycle >> 8) & 0xFF;
                state.settings.raw = nvm_getSettings();
                if(state.settings.fields.mqttSetting == 1){
                    state.mqttState = ENABLED;
                }
                
                refreshState();
                ui_printBootMenu();
                __delay_ms(2000);
                ui_printHeader();
                ui_printMenu();
                ui_refreshHeader(&state);
                state.loopState = IDLE;
                break;
            case IDLE:
                if(state.mqttState == ENABLED){
                    state.loopState = CONNECTING;
                }
                else if(state.flags.bChange){
                    state.loopState = BROWSE;
                }
                else if(state.flags.rxPacket == 1){
                    state.flags.rxPacket = 0;
                    state.loopState = HANDLE_MSG;
                }
                else if(state.flags.refresh == 1){
                    state.flags.refresh = 0;
                    state.loopState = REFRESH;
                }
                else{
                    Idle(); // Woken on interrupts
                }
                break;
            case CONNECTING:; // Some weird C99 grammar quirk
                uint8_t connected = mqtt_connect(&state, 120, packet);
                if(connected){
                    state.mqttState = CONNECTED;
                    state.loopState = SUBSCRIBE;
                }
                else{
                    state.mqttState = DISCONNECTED;
                    state.loopState = IDLE;
                }
                break;
            case SUBSCRIBE:; // Some weird C99 grammar quirk
                uint8_t subscribed = 0; 
                subscribed  = mqtt_subscribe(&state, NEWSUNRISE, packet);
                subscribed &= mqtt_subscribe(&state,  NEWSUNSET, packet);
                if(subscribed){
                    state.loopState = PUB_STATE;
                }
                else{
                    state.loopState = SUBSCRIBE;
                }
                break;
            case REFRESH:
                refreshState();
                ui_refreshHeader(&state);
                if(state.mqttState == CONNECTED){
                    state.loopState = PUB_VALS;
                }
                else{
                    state.loopState = IDLE;
                }
                break;
            case BROWSE:; // C99 grammar quirk
                uint8_t printMenu = 0;
                switch(ui_browse(&state)){
                    case NOUPDATES:
                        state.loopState = IDLE;
                        printMenu = 1;
                        break;
                    case UPDATETIME:
                        rtc_setTime(state.time.hour, state.time.min);
                        util_runLampFSM(&state);
                        if(state.mqttState == CONNECTED){
                            state.loopState = PUB_STATE;
                        }
                        else{
                            state.loopState = IDLE;
                        }
                        printMenu = 1;
                        break;
                    case UPDATENODEID:
                        nvm_saveSettings(state.settings.raw);
                        if(state.mqttState == DISABLED){
                            state.loopState = IDLE;
                        }
                        else{
                            mqtt_disconnect();
                            state.loopState = CONNECTING;
                        }
                        printMenu = 1;
                        break;
                    case UPDATECYCLE:
                        nvm_saveCycle(state.sunrise, state.sunset);
                        util_runLampFSM(&state);
                        if(state.mqttState == CONNECTED){
                            state.loopState = PUB_STATE;
                        }
                        else{
                            state.loopState = IDLE;
                        }
                        printMenu = 1;
                        break;
                    case UPDATEMQTT:
                        if(state.mqttState == DISABLED){
                            mqtt_disconnect();
                            state.loopState = REFRESH;
                        }
                        else{
                            state.loopState = IDLE;
                        }
                        printMenu = 1;
                        break;
                    case UPDATEINDEX:
                        state.loopState = IDLE;
                    default:
                        state.loopState = IDLE;
                        break;    
                }
                state.flags.bChange = 0;
                if(printMenu){
                    ui_printHeader();
                    ui_printMenu();
                    ui_refreshHeader(&state);
                }
                break;
            case PUB_VALS:
                mqtt_pubTemp(state.boardTemp, state.settings.fields.nodeID, BOARDTEMP);
                mqtt_pubTemp(state.plantTemp, state.settings.fields.nodeID, PLANTTEMP);
                mqtt_pubWaterLevel(state.waterLevel, state.settings.fields.nodeID, WATER);
                state.loopState = IDLE;
                break;
            case PUB_STATE:
                mqtt_pubCycle(state.sunrise, state.settings.fields.nodeID, SUNRISE);
                mqtt_pubCycle(state.sunset, state.settings.fields.nodeID, SUNSET);
                mqtt_pubLampState(state.lampState, state.settings.fields.nodeID, LAMPSTATE);
                state.loopState = REFRESH;
                break;
            case HANDLE_MSG:
                state.flags.rxPacket = 0;

                // Look for messages on NEWSUNRISE or NEWSUNSET topics:
                if(packet[MTYPE_I] == PUBLISH){
                    if(packet[PUB_TOP_I] == NEWSUNRISE){
                        state.sunrise = packet[PUB_DATA_I];
                        nvm_saveCycle(state.sunrise, state.sunset);
                        util_runLampFSM(&state);
                    }
                    else if(packet[PUB_TOP_I] == NEWSUNSET){
                        state.sunset = packet[PUB_DATA_I];
                        nvm_saveCycle(state.sunrise, state.sunset);
                        util_runLampFSM(&state);
                    }
                    state.loopState = PUB_STATE;
                }
                else{
                    state.loopState = IDLE;
                }
                break;
            default:
                break;
        }
    }
    return 0;
}

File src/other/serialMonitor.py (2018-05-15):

import serial
from time import sleep
port = input("Enter port: ")

ser = serial.Serial(port, 9600)

#sleep(2)
#print('Sending hello world...')

##  7E 00 19 10 01 00 00 00 00 00 00 00 00 FF FE 00 00 48 45 4C 4C 4F 20 57 4F 52 4C 44 D5
#hw = b"\x7E\x00\x19\x10\x01\x00\x00\x00\x00\x00\x00\x00\x00\xFF\xFE\x00\x00\x48\x45\x4C\x4C\x4F\x20\x57\x4F\x52\x4C\x44\xD5"
#ser.write(hw)

while True:
    a = ser.read()
    print(hex(int.from_bytes(a,byteorder='little')), end = ' ' )

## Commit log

2018-05-15 Add files from old project
    [XBee_RPi_breakout.brd, XBee_RPi_breakout.sch, nodeBoard.brd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]
2018-05-15 Change from periodic timer to RTC alarm
2018-05-21 Add CONNACK frame
2018-05-21 Make UART continue in IDLE mode
2018-05-21 Add small delay when sending frames for stability
    [xbee.c]
2018-05-21 Add functions for publishing sensor values
2018-05-21 Add start and stop functions for Timer 2/3
2018-06-13 Add PowerBoard eagle project
    [PowerBoard.sch]
2018-07-16 Backup changes
    [PiZero_breakout.brd, PiZero_breakout.sch, XBee_RPi_breakout.brd]
